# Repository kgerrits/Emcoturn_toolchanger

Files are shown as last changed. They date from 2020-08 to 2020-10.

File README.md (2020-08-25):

# Emcoturn_toolchanger
Toolchanger PCB and firmware for Emcoturn 120/220 lathe

This is a PCB to control the 8-position tool turrent for the EmcoTurn 120 and 220 lathe. Currently it uses modbus over RS485 communication.

Specifications:
* Teensy 3.2 for the control logic
* 24VDC power supply. Internal 5V 2A switching regulator
* TI DRV8876 to control the maxon DC motor in the turret
* Locked position detected by stall current of motor
* 4 additional IO's on the board for free to program functions

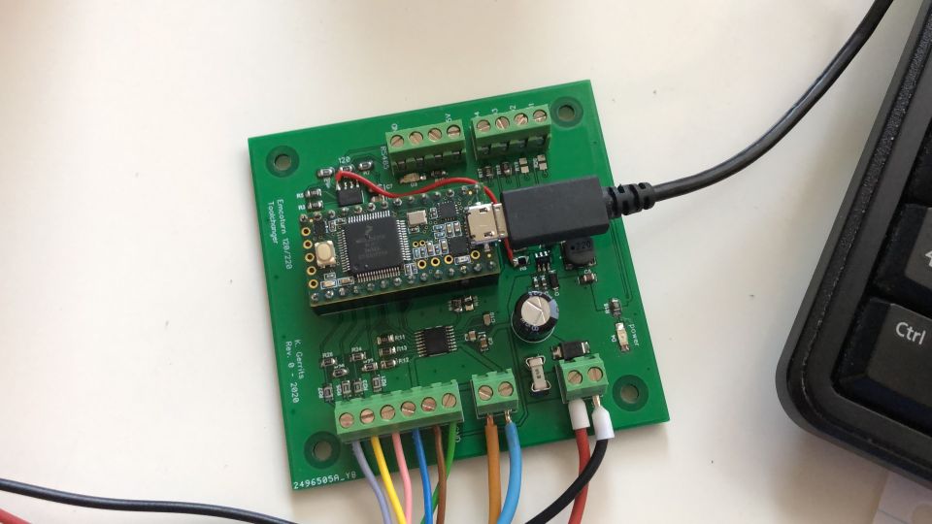
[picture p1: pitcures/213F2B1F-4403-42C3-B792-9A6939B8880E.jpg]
Emcoturn toolchanger picture


Testrun of the PCB:

(https://www.youtube.com/watch?v=sjd6qg67e3A)

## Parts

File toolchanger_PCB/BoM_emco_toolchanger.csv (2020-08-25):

RefDes | Value | Name | Manufacturer | Quantity | Description
C1 | 100nF | CAP_0805 |  | 1
C2 | 82uf | 63ZLJ82M8X11.5 | Rubycon | 1
C3, C4 | 1uF | CAP_0603 |  | 2
C5 | 22uF | CAP_0805 |  | 1
C6 | 10uF | CAP_0805 |  | 1
C7, C8 | 0.1uF | CAP_0805 |  | 2
C9 | 0.1uF | CAP_0603 |  | 1
C10 | 0.022uF | CAP_0603 |  | 1
D1 | 550mV / 2A | DIODE_0805 |  | 1
D2 | 26V | SMBJ26A | Littelfuse | 1
D3, D4 |  | SMD_LED | 2099245 | 2 | LED
F1 | 0157004.DR | FUSE | Littelfuse | 1 | Fuse
J1, J3 |  | Screw PCB 2-way | Multicomp | 2
J2, J5 |  | Screw PCB 4-way | Multicomp | 2
J4 |  | Screw PCB 6-way | Multicomp | 1
L1 | 22uH | IND_0805 |  | 1
MCU1 |  | Teensy 3.2 | PJRC | 1
R1 | 120 | RES_0805 |  | 1
R2, R3, R5, R11, R17, R18, R19, R20 | 10K | RES_0805 |  | 8
R6 | 111k | RES_0805 |  | 1
R7, R9, R21, R23, R25, R27 | 20K | RES_0805 |  | 6
R8 | 20k | RES_0805 |  | 1
R10, R16 | 100 | RES_0805 |  | 2
R12, R14, R15 | 0 | RES_0805 |  | 3
R13 | 1.18K | RES_0805 |  | 1
R22, R24, R26, R28 | 3.15K | RES_0805 |  | 4
U1 |  | LMR14010ADDC | Texas Instruments | 1
U2 |  | Max485 |  | 1
U3 |  | DRV8876 | Texas Instruments | 1
 |  |  |  | 52

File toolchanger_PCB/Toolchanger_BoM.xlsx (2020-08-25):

Bill of Materials - Component List
EMCOTurn 120 toolchanger PCB
RefDes | Value | Name | Manufacturer | QTY | Description | Supplier | Supplier PN | Price | Price/PCB
C1 | 100nF | CAP_0805 |  | 1 | SMD multilayer ceramic capacitor | Farnell | 1759265 (https://nl.farnell.com/multicomp/mc0805b104k500ct/cap-0-1-f-50v-10-x7r-0805/dp/1759265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) | €0.14 | €0.14
C2 | 82uf | 63ZLJ82M8X11.5 | Rubycon | 1 | Electrolytic capacitor | Farnell | 2346476 (https://nl.farnell.com/rubycon/63zlj82m8x11-5/cap-82-f-63v-20/dp/2346476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) | €0.35 | €0.35
C3, C4 | 1uF | CAP_0603 |  | 2 | SMD multilayer ceramic capacitor | Farnell | 9227776 (https://nl.farnell.com/kemet/c0603c105k8pactu/cap-1-f-10v-10-x5r-0603/dp/9227776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) | €0.08 | €0.16
C5 | 22uF | CAP_0805 |  | 1 | SMD multilayer ceramic capacitor | Farnell | 1907510 (https://nl.farnell.com/murata/grm21br61e226me44l/cap-22-f-25v-20-x5r-0805/dp/1907510?scope=partnumberlookahead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) | €0.52 | €0.52
C6 | 10uF | CAP_0805 |  | 1 | SMD multilayer ceramic capacitor | Farnell | 1463362 (https://nl.farnell.com/kemet/c0805c106k8pactu/cap-10-f-10v-10-x5r-0805/dp/1463362) | €0.16 | €0.16
C7, C8 | 0.1uF | CAP_0805 |  | 2 | SMD multilayer ceramic capacitor | Farnell | 2581082 (https://nl.farnell.com/kemet/c0805c104z5vactu/cap-0-1-f-50v-y5v-0805/dp/2581082) | €0.06 | €0.12
C9 | 0.1uF | CAP_0603 |  | 1 | SMD multilayer ceramic capacitor | Farnell | 2470450 (https://nl.farnell.com/murata/grm033r61a104ke15d/cap-0-1-f-10v-10-x5r-0201/dp/2470450) | €0.06 | €0.06
C10 | 0.022uF | CAP_0603 |  | 1 | SMD multilayer ceramic capacitor | Farnell | 2434636 (https://nl.farnell.com/murata/grm0335c1e220ja01d/cap-22pf-25v-5-c0g-np0-0201/dp/2434636) | €0.02 | €0.02
D1 | 550mV / 2A | DIODE_0805 |  | 1 | Schottkey rectifier | Farnell | 2822567 (https://nl.farnell.com/on-semiconductor/ss26fl/schottky-rect-aec-q101-60v-sod/dp/2822567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) | €0.27 | €0.27
D2 | 26V | SMBJ26A | Littelfuse | 1 | TVS Diode | Farnell | 2981361 (https://nl.farnell.com/taiwan-semiconductor/smbj26a/tvs-diode-600w-26v-unidir-do-214aa/dp/2981361?st=SMBJ26A) | €0.27 | €0.27
D3, D4 |  | SMD_LED | Kingbright | 2 | Surface mount LED red | Farnell | 2099245 (https://nl.farnell.com/kingbright/kpt-3216ec/led-1206-red-15mcd-625nm/dp/2099245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) | €0.12 | €0.25
F1 | 0157004.DR | FUSE | Littelfuse | 1 | surface mount fuse | Farnell | 1702515 (https://nl.farnell.com/littelfuse/0157004-dr/fuse-smd-4a-omni-block-very-fast/dp/1702515?st=0157004.DR) | €2.67 | €2.67
J1, J3 |  | Screw PCB 2-way | Multicomp | 2 | Wire-to-Board terminal block 2-way | Farnell | 2007985 (https://nl.farnell.com/multicomp/mc000018/terminal-block-wire-to-brd-2pos/dp/2007985?scope=partnumberlookahead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) | €0.53 | €1.06
J2, J5 |  | Screw PCB 4-way | Multicomp | 2 | Wire-to-Board terminal block 4-way | Farnell | 2007987 (https://nl.farnell.com/multicomp/mc000020/terminal-block-wire-to-brd-4pos/dp/2007987?scope=partnumberlookahead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) | €1.05 | €2.10
J4 |  | Screw PCB 6-way | Multicomp | 1 | Wire-to-Board terminal block 6-way | Farnell | 2007991 (https://nl.farnell.com/multicomp/mc000022/terminal-block-wire-to-brd-6pos/dp/2007991?scope=partnumberlookahead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) | €1.60 | €1.60
L1 | 22uH | IND_0805 |  | 1 | Power inductor | Farnell | 2493045 (https://nl.farnell.com/tdk/vls6045ex-220m/inductor-22uh-1-9a-20-wirewound/dp/2493045?scope=partnumberlookahead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) | €0.61 | €0.61
MCU1 |  | Teensy 3.2 | PJRC | 1 |  |  |  |  | €0.00
R1 | 120 | RES_0805 |  | 1 | SMD resistor | Farnell | 2303452 (https://nl.farnell.com/panasonic/erj6enf1200v/res-120r-1-0-125w-0805-thick-film/dp/2303452) | €0.10 | €0.10
R2, R3, R5, R11, R17, R18, R19, R20 | 10K | RES_0805 |  | 8 |  | Farnell | 9234136 (https://nl.farnell.com/yageo/rc0805jr-0710kl/res-10k-5-0-125w-0805-thick-film/dp/9234136) | €0.04 | €0.28
R6 | 111k | RES_0805 |  | 1 |  | Farnell | 1469864 (https://nl.farnell.com/vishay/crcw0805110kfkea/res-110k-1-0-125w-0805-thick-film/dp/1469864) | €0.08 | €0.08
R7, R8, R9, R21, R23, R25, R27 | 20K | RES_0805 |  | 7 | SMD Thick film resistor | Farnell | 2447603 (https://nl.farnell.com/multicomp/mcwr08x2002ftl/res-20k-1-0-125w-0805-thick-film/dp/2447603) | €0.01 | €0.05
R10, R16 | 100 | RES_0805 |  | 2 | SMD Thick film resistor | Farnell | 9237364 (https://nl.farnell.com/yageo/rc0805fr-07100rl/res-100r-1-0-125w-0805-thick-film/dp/9237364) | €0.05 | €0.09
R12, R14, R15 | 0 | RES_0805 |  | 3 | SMD jumper resistor | Farnell | 2057661 (https://nl.farnell.com/panasonic/erj6gey0r00v/res-0r0-0-125w-0805-thick-film/dp/2057661?MER=sy-me-pd-mi-alte) | €0.04 | €0.11
R13 | 1.18K | RES_0805 |  | 1 | SMD Thick film resistor | Farnell | 2303558 (https://nl.farnell.com/panasonic/erj6enf1181v/res-1k18-1-0-125w-0805-thick-film/dp/2303558) | €0.09 | €0.09
R22, R24, R26, R28 | 3.15K | RES_0805 |  | 4 | SMD Thick film resistor | Farnell | 2303602 (https://nl.farnell.com/panasonic/erj6enf3161v/res-3k16-1-0-125w-0805-thick-film/dp/2303602) | €0.09 | €0.37
U1 |  | LMR14010ADDC | Texas Instruments | 1 | Switching voltage regulator | Mouser | 595-LMR14010ADDCR (https://nl.mouser.com/ProductDetail/Texas-Instruments/LMR14010ADDCR) | €2.10 | €2.10
U2 |  | Max485 |  | 1 | RS-485 tranceiver | Mouser | 700-MAX485EESAT (https://nl.mouser.com/ProductDetail/Maxim-Integrated/MAX485EESA%2bT) | €3.34 | €3.34
U3 |  | DRV8876 | Texas Instruments | 1 | H-bridge motor driver | Mouser | 595-DRV8876PWPT (https://nl.mouser.com/ProductDetail/Texas-Instruments/DRV8876PWPT?qs=T3oQrply3y%2FSI4rysKckzA%3D%3D) | €2.08 | €2.08
 |  |  |  |  |  |  |  | TOTAL: | €19.06

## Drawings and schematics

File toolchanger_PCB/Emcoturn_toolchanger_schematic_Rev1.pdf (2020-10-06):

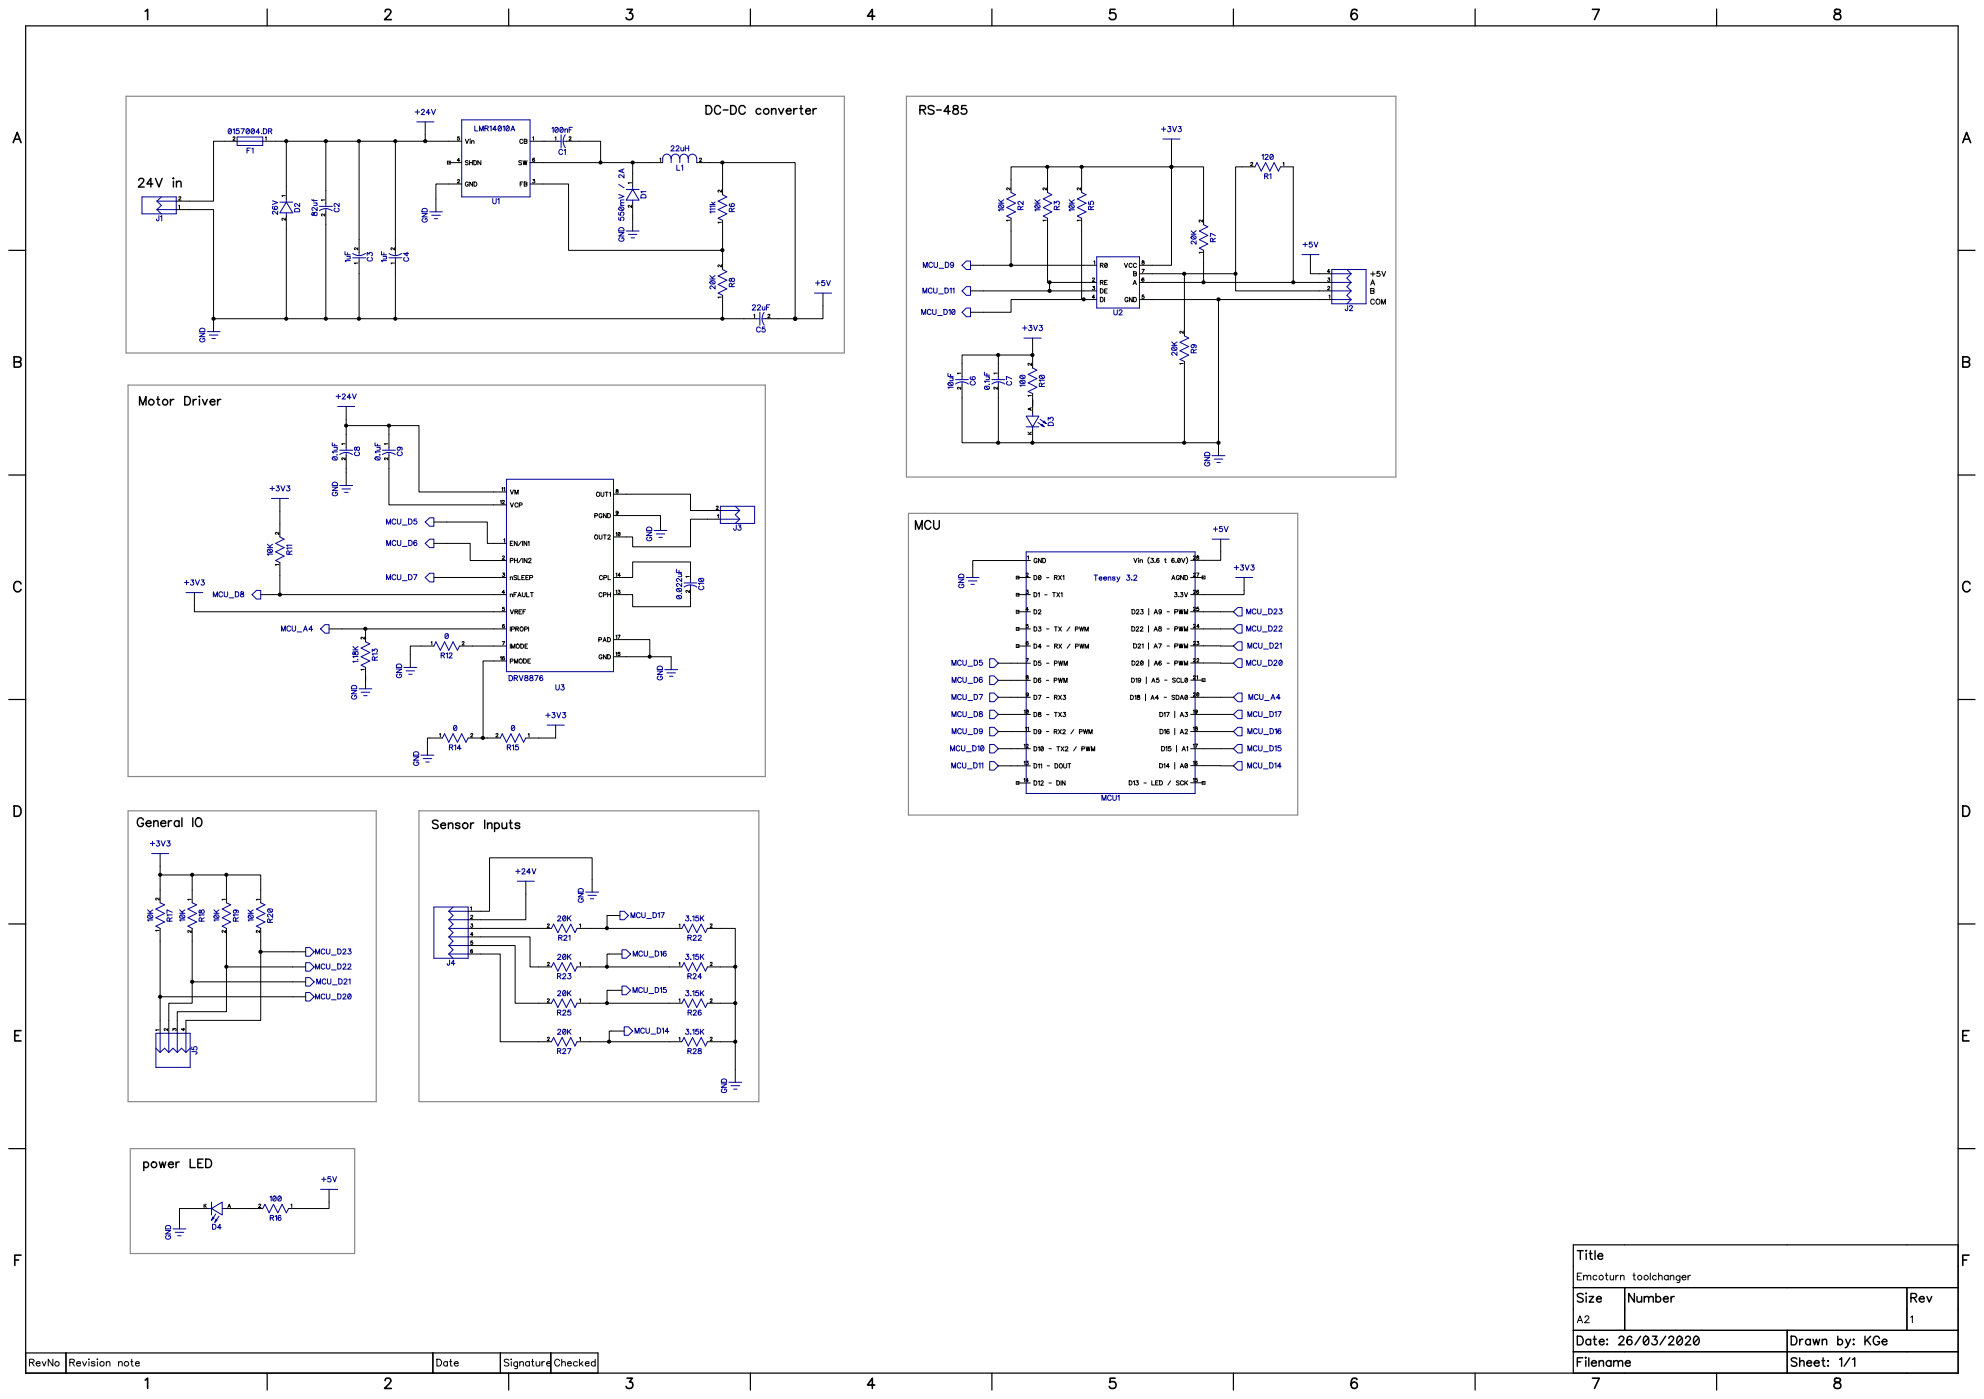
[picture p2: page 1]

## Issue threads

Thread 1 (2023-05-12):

Teensy 3.2 Shortatge

arquecc, 2023-05-12:
Hi there,

I'm facing an issue with the Teensy 3.2 as it appears that it will no longer be available and the manufacturer recommends using the Teensy 4.0 instead. I'm wondering if it's possible to modify the PCB to adapt to the Teensy 4.0. Could you please advise on this matter?

Thank you!

kgerrits, 2023-05-12:
Hi,

I think this should be not too much work. I will look into this coming week.

Closed 2023-05-12.

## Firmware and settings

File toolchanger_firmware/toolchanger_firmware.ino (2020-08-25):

#include <Metro.h>

// Firmware version
const char FirmVer[] = "V1.00";

// --------------------------------------------------------------------------------------------------------------------
// Pin definition
// --------------------------------------------------------------------------------------------------------------------
const int MIN1 = 5;
const int MIN2 = 6;
const int MSLEEP = 7;
const int MFB = A4;
const int MFAULT = 8;
const int LEDPIN = 13;
const int S4 = 17;
const int S3 = 16;
const int S2 = 15;
const int S1 = 14;
const int TX2PIN = 10; // serial 2 transmit pin
const int RX2PIN = 9; // serial 2 receive pin
const int TEPIN = 11; // transmit enable
const int ENAPIN = 23;

// --------------------------------------------------------------------------------------------------------------------
// Timer variables
// --------------------------------------------------------------------------------------------------------------------
const int SampleTimeSignalConditioning = 5; // [ms]
const int SampleTimeDisplayValues = 100; // [ms]
const int SampleTimeStateMachine = 5; // [ms]
unsigned long backingDelayStart;
int backingDelay = 120; // [ms]
unsigned long backingTimeoutStart;
int backingTimeout = 1000; // [ms] maximum time of full backwards motor current
long toolchangeStartTime = 0;

// declare timer objects
Metro signalConditioningTimer = Metro(SampleTimeSignalConditioning);
Metro displayValuesTimer = Metro(SampleTimeDisplayValues);
Metro stateMachineTimer = Metro(SampleTimeStateMachine);


// declare toolchange state variables
int state;
#define STATE_INIT 0
#define STATE_ADVANCE_TOOL 1
#define STATE_BACKING_DELAY 2
#define STATE_ENGAGE_RATCHET 3
#define STATE_HOLDING_CURRENT 4
#define STATE_CONFIRM_TOOL 5
#define STATE_HOMING 6

// --------------------------------------------------------------------------------------------------------------------
// declare variables
// --------------------------------------------------------------------------------------------------------------------
unsigned int motorMode = 0;
int motorCurrent = 0;
int motorPWMLimit = 2000;
int MotorPWM = 0;
int rawCurrent = 0;
float alphaCurrent = 0.01;
float filteredCurrent = 0;
float lastCurrentFilt = 0;
boolean positionState[4];
const int positionSensor[4] = {S1, S2, S3, S4};
int toolNo = 0;
int toolRequest;
int lastToolRequest;
int toolConfirm;
boolean toolChangerEnabled = false;
boolean _toolChangerEnabled = false; // previous toolChangerEnabled state
boolean homingRequired = true;  // when enable is toggled, homing of the toolchanger is required.
boolean startHoming = false;

// motor PWM commands
const int motorAdvancePWM = 2000;
const int motorBackupPWM = -2000;
const int motorHoldingPWM = -200;


// serial communication variables
const byte numChars = 32;
char receivedChars[numChars];
char tempChars[numChars];        // temporary array for use when parsing
// variables to hold the parsed data
char messageFromPC[numChars] = {0};
int integerFromPC = 0;
float floatFromPC = 0.0;
boolean newData = false;

// modbus communication variables
#define ID   1                // slave ID
#define HWSERIAL Serial2

byte frameBuffer[256];
const unsigned int t35 = 750; // [us] specified in modbus protocol for baud > 19200
const unsigned int t15 = 550;  // [us] specified in modbus protocol for baud > 19200
unsigned long modbusT35TimerStart;
unsigned long modbusT15TimerStart;
byte frameLength = 0;
boolean frameOK = false;
boolean frameChecked = false;
const byte modbusResponseWMRLength = 8;
byte modbusResponseWMR[modbusResponseWMRLength]; // buffer containing response for modbus Write Multiple Registers
byte modbusResponseRHR[256]; // buffer containing response for modbus Read Holding Registers (length is depending on request, so set to max message length)
byte modbusResponseRDI[256]; // buffer containing response for modbus Read Discrete Inputs (length is depending on request, so set to max message length)
byte modbusResponseWSR[8]; 
byte modbusResponseWSC[8];
boolean RDI_states[32]; // array containing discrete states to be read through modbus 

// modbus receive function state variables
byte modbusReceiveState;
#define MB_STATE_INIT 0
#define MB_STATE_IDLE 1
#define MB_STATE_RECEPTION 2
#define MB_STATE_CONTROL_WAITING 3

// modbus process function state variables
byte modbusFunctionCode;
#define FC_READ_MULTIPLE_COILS 1
#define FC_READ_DISCRETE_INPUTS 2
#define FC_READ_HOLDING_REGISTERS 3
#define FC_READ_INPUT_REGISTER 4
#define FC_WRITE_SINGLE_COIL 5
#define FC_WRITE_SINGLE_REGISTER 6
#define FC_WRITE_MULTIPLE_COILS 15
#define FC_WRITE_MULTIPLE_REGISTERS 16
#define FC_REPORT_SLAVEID 17

void setup() {
  // set pinmodes
  pinMode(MIN1, OUTPUT);
  pinMode(MIN2, OUTPUT);
  pinMode(MSLEEP, OUTPUT);
  pinMode(MFB, INPUT);
  pinMode(MFAULT, INPUT);
  pinMode(LEDPIN, OUTPUT);
  pinMode(ENAPIN, INPUT);

  // ADC setup
  analogWriteFrequency(5, 20000); // change PWM to inaudible 20 kHz
  analogWriteFrequency(6, 20000); // change PWM to inaudible 20 kHz
  analogWriteResolution(11);  // analogWrite value 0 to 1023, or 1024 for high

  // disable motor
  digitalWrite(MIN1, LOW);
  digitalWrite(MIN2, LOW);
  analogWrite(MIN1, 0);
  digitalWrite(MSLEEP, LOW);

  // attach interrupts for sensor pins
  attachInterrupt(S1, readSensor0, CHANGE);
  attachInterrupt(S2, readSensor1, CHANGE);
  attachInterrupt(S3, readSensor2, CHANGE);
  attachInterrupt(S4, readSensor3, CHANGE);

  // get initial sensor reading
  positionState[0] = digitalRead(S1);
  positionState[1] = digitalRead(S2);
  positionState[2] = digitalRead(S3);
  positionState[3] = digitalRead(S4);
  positionDecode(positionState);

  // initial tool request
  toolRequest = -1; // state machine init state (wait for command)

  // Setup serial communication
  Serial.begin(115200);

  // Setup modbus communication
  Serial2.setTX(TX2PIN);
  Serial2.setRX(RX2PIN);
  Serial2.transmitterEnable(TEPIN);
  HWSERIAL.begin(115200, SERIAL_8N2); // 115200 baud, 8-data-bits, no-parity, 2 stop bits

  // fill known data for modbus responses
  modbusResponseWMR[0] = ID;
  modbusResponseWMR[1] = FC_WRITE_MULTIPLE_REGISTERS;
  modbusResponseRHR[0] = ID;
  modbusResponseRHR[1] = FC_READ_HOLDING_REGISTERS;
  modbusResponseWSR[0] = ID;
  modbusResponseWSR[1] = FC_WRITE_SINGLE_REGISTER;
  modbusResponseWSC[0] = ID;
  modbusResponseWSC[1] = FC_WRITE_SINGLE_COIL;
  modbusResponseRDI[0] = ID;
  modbusResponseRDI[1] = FC_READ_DISCRETE_INPUTS;
  

  modbusReceiveState = STATE_INIT;
  modbusT35TimerStart = micros();

  Serial.println("Setup complete.");
}

void loop() {

  // serial communication
  recvWithStartEndMarkers();
  if (newData == true) {
    strcpy(tempChars, receivedChars);
    // this temporary copy is necessary to protect the original data
    //   because strtok() used in parseData() replaces the commas with \0
    parseData();
    doParsedData();
    newData = false;
  }

  // modbus communication
  modbusReceive(); // watch for incoming messages

  // display message when available
  if (frameLength > 0 && modbusReceiveState == MB_STATE_IDLE) {
    // process modbus message
    modbusProcess();
  }

  // set motorPWM on each loop cycle
  TurretMotor(MotorPWM);

  // check for ellapsed timers
  if (displayValuesTimer.check() == 1) {
//    displayValues();
  }
  if (signalConditioningTimer.check() == 1) {
    signalConditioning();
    updateRDI_states();
  }
  if (stateMachineTimer.check() == 1) {
    StateMachineToolchange();
  }

}

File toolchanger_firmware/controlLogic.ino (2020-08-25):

void StateMachineToolchange() {
  switch (state) {

    case STATE_INIT:
      // no tool engaged
      MotorPWM = 0;

      if (toolRequest != toolConfirm && toolRequest != -1 && homingRequired == false && toolChangerEnabled == true) {
        toolchangeStartTime = millis(); // monitor time taken for toolchange
        state = STATE_ADVANCE_TOOL;
      }

      if (homingRequired == true && toolChangerEnabled == true && startHoming == true) {
        toolchangeStartTime = millis(); // monitor time taken for toolchange
        state = STATE_HOMING;
      }

      break;

    case STATE_ADVANCE_TOOL:
      // move tool forwards
      MotorPWM = motorAdvancePWM;

      if (toolRequest == toolNo) {
        backingDelayStart = millis();
        state = STATE_BACKING_DELAY;
      }
      break;

    case STATE_BACKING_DELAY:
      // wait to fully pass ratched before backing up
      MotorPWM = motorAdvancePWM;

      if (millis() - backingDelayStart >= backingDelay && toolRequest == toolNo) {
        backingTimeoutStart = millis();
        state = STATE_ENGAGE_RATCHET;
      }
      break;

    case STATE_ENGAGE_RATCHET:
      // move backwards until ratchet engaged
      MotorPWM = motorBackupPWM;

      if (millis() - backingTimeoutStart >= backingTimeout) {
        Serial.println("Toolchange error!");
        state = STATE_INIT;
      }

      if (filteredCurrent < -110) {
        // ratchet engaged
        state = STATE_HOLDING_CURRENT;
      }
      break;

    case STATE_HOLDING_CURRENT:
      // lower PWM to keep ratchet engaged
      {
        MotorPWM = motorHoldingPWM;
        long timeTaken = millis() - toolchangeStartTime;

        toolConfirm = toolRequest;
        Serial.print("completed in: ");
        Serial.print(timeTaken);
        Serial.print("[ms] | Active tool: ");
        Serial.println(toolConfirm);
        state = STATE_CONFIRM_TOOL;

      }
      break;

    case STATE_CONFIRM_TOOL:
      // desired tool position reached
      MotorPWM = motorHoldingPWM;

      if (toolRequest != toolConfirm && homingRequired == false) {
        toolchangeStartTime = millis(); // monitor time taken for toolchange
        state = STATE_ADVANCE_TOOL;
      }

      if (toolConfirm == 1 && homingRequired == true) {
        // confirmed tool equals homing tool. Set homing required flag to false
        homingRequired = false;
        startHoming  = false;
        Serial.println("Homing complete");
      }

      break;

    case STATE_HOMING:
      // perform homing routine
      // homing --> goto tool 1
      Serial.println("Start homing...");
      toolRequest = 1;
      state = STATE_ADVANCE_TOOL;
      break;

  }

  // check toolchanger enable conditions

  if (toolChangerEnabled == true && _toolChangerEnabled != toolChangerEnabled) {
    MotorPWM = 0;
    digitalWrite(MSLEEP, HIGH);  // enable motor driver
    digitalWrite(LEDPIN, HIGH);
    Serial.println("Toolchanger enabled");
  }
  else if (toolChangerEnabled == false && _toolChangerEnabled != toolChangerEnabled) {
    state = STATE_INIT;
    MotorPWM = 0;
    digitalWrite(MSLEEP, LOW);  // disable motor driver
    digitalWrite(LEDPIN, LOW);
    Serial.println("Toolchanger disabled");
  }

  if (toolChangerEnabled == true && _toolChangerEnabled == false) {
    Serial.println("Homing required");
    homingRequired = true;
  }
  _toolChangerEnabled = toolChangerEnabled; // remember previous state of toolchanger enable
}

boolean validateToolRequest(int request) {
  // Toolchanger has 8 positions, if toolrequest >8 is received, it will be modulo 8.
  // If request is valid, tool position 1-8 will be returned
  // If request is invalid, -1 will be returned.

  if (request <= 0) {
    return false;
  }
  else {
    int toolRangeMapped = request % 8;

    if (toolRangeMapped == 0) {
      toolRangeMapped = 8; //--> multiple of 8 % 8 = 0 --> meaning if answer is 0, tool 8 must be called
    }

    if (toolRangeMapped > 0 && toolRangeMapped <= 8) {
      // double check if tool is in range of toolchanger
      toolRequest = toolRangeMapped;
      return true;
    }
    else {
      return false;
    }

  }

}

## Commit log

2020-08-25 Add PCB files
    [BoM_emco_toolchanger.csv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]
2020-10-06 Add PCB schematic pdf
